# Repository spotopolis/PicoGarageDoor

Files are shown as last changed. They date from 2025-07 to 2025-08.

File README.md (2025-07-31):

# PicoGarageDoor
Simple garage door opener controlled wirelessly via webpage

# Intro
This is a simple device that allows you to add wireless functionality to garage door control.
This project was a result of being a motorcycle rider and wanting to be able to open/close the garage to pull the bike in/out without having to either walk back into the house to open/close the garage or press the paired garage door controller button attached to the sun visor in my car. I do not have a garage door button panel outside of my garage, so I made this simple device to access the garage door from my phone while within my homes WiFi signal range.

# Parts list

Required:

Raspberry Pi Pico W [from Microcenter](https://www.microcenter.com/product/687384/raspberry-pi-pico-2-w) (( Should also work with a Pico 2W but has not been tested ) $6.99 USD at the time of writing )

Arduino v5 relay [from MicroCenter](https://www.microcenter.com/product/659887/inland-single-5v-relay-module-for-arduino) ($1.99 USD at the time of writing)

Project can be completed for under $10 USD with just these two components and some spare wire.
#

Optional:

To make the build a litle cleaner, use GPIO headers and some jumper wires.

Jumper wires [from Microcenter](https://www.microcenter.com/product/412198/leo-sales-ltd-jumpers,-premium-6-f-f,-50-wires) ( $14.99 USD at the time of writing )

GPIO right-angle header(s) [from Microcenter](https://www.microcenter.com/product/475249/schmartboard-inc-01-spacing-40-single-row-right-angle-headers-10-pack) ( $7.99 USD at the time of writing )

# Function
The PicoW hosts a small basic webserver via the code below:



This in turn serves the following webpage:

GDoor

The blue "Open/Close" button acts as a momentary switch to trigger a 5v relay attached directly to the PicoW via GPIO.

This function is handled here:



#

I discovered that during a power outage or power flicker during a storm, while the WiFi network and PicoW would come back online after power is restored, the PicoW would lose connection to the network and therefor could not host the webpage to interact with. It would only come back up if I power cycled the PicoW again by hand. So to try and fix this, I have also included some basic logic to test if the connection to the gateway is active, if it is not, it will reboot the PicoW to try and reestablish a connection.

The PicoW will wait initially 60 seconds on first boot before testing that the network is active to give the device time to connect. After 60 seconds, the PicoW will start to ping the gateway every 30 seconds. If the ping attempt fails, it will retry to ping the gateway 2 more times (3 in total) before triggering the reboot. This is to help mitigate any temp signals issues / interference along with the PicoW's lack of power to reboot on a false positive signal interruption. This code is handled here:



and here:



# Setup

Before uploading the main.py to the PicoW, edit the file at lines 7, 8, and 9. Fill in your SSID, password, and gateway IP. Thonny or NotePad++ can be used for the edits.



Connections between the PicoW and relay are:

PicoW: VBUS <----> Relay: V

PicoW: GND  <----> Relay: G

PicoW: GP18 <----> Relay: S

#

Connect any 5v 1a USB charger to the PicoW's micro-USB port to power it on. Once the PicoW is powered on, it should get a local IP address assigned via DHCP from your firewall/router. You will want to log into your firewall/router and assign the PicoW a static IP address to make sure it doesn’t change on you and is always at the IP address you are expecting.

Once you select and set a static IP address for the PicoW in your firewall/router, power cycle the PicoW so it connects to your network with the newly assigned static IP.

Open a web browser on any device connected to the same WiFi network as the PicoW and browse to that static IP address. You should see the same page that I showed above under the "Function" section of this page. Tap or click the blue "Open/Close" button to verify the relay is triggering. You should hear it click on and then off while also getting an accompanying red LED to flash on the relay. If so, you are all set and ready to disconnect and attach it to your existing garage door button.

#

gdoor3

The relay can then be connected to your existing 2 wire garage door button via jumpers so that the button can still function while the relay is attached.
All this device is doing is acting like a 2nd garage door button attached to the same door. The garage door button is a momentary switch that seperates ( or bridges ) the connection between the two wires. By running jumper wires from the existing button to the relay, you are allowing a second button/switch ( the relay ) to trigger this function as well. Only instead of a physical button press, it is done via touchscreen on a mobile device on a private LAN hosted wepbage.

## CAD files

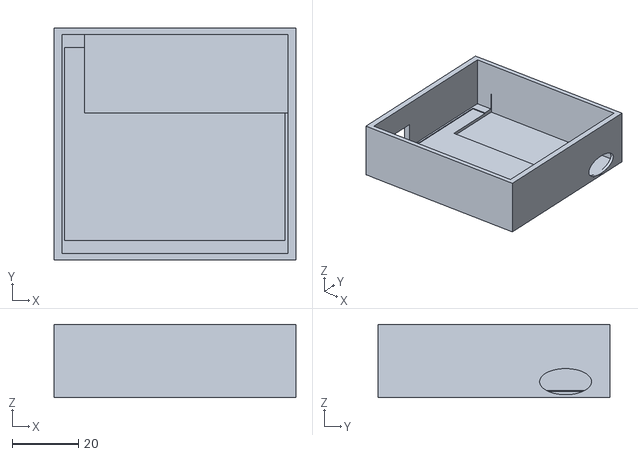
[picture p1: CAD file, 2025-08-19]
Box_Obj_Part.stl
72.9 x 69.8 x 22.0

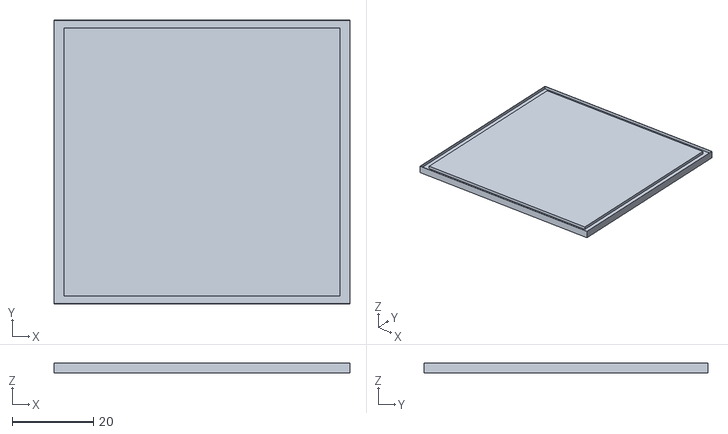
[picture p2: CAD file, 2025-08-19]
Lid_Obj_Part.stl
73.0 x 70.0 x 2.50

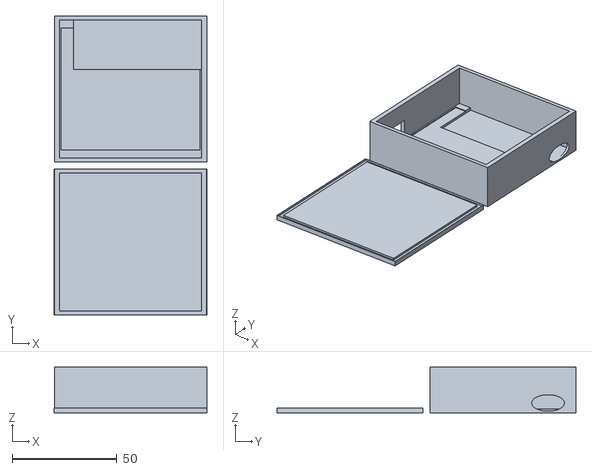
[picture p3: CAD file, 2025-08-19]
PicoW_Relay_Box_AIO.stl
73.0 x 143.0 x 22.0

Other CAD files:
PicoW_Relay_Box_ProjectFile.3mf

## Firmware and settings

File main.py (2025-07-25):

from machine import Pin, reset, Timer
import network
import time
import usocket as socket

# Wi-Fi credentials
SSID = "YOUR_WIFI_NAME_HERE"
PASSWORD = "WIFI_PASSWORD_HERE"
GATEWAY_IP = "ROUTER_IP_ADDRESS_USUALLY_192.168.1.1_OR_SIMILAR"

# Relay and onboard LED setup
relay = Pin(18, Pin.OUT)
led = Pin("LED", Pin.OUT)

# Flash LED on boot
led.on()
time.sleep(0.5)
led.off()

# Connect to Wi-Fi
wlan = network.WLAN(network.STA_IF)
wlan.active(True)
wlan.connect(SSID, PASSWORD)

# Wait up to 60s for Wi-Fi
start = time.time()
while wlan.status() != 3 and (time.time() - start) < 60:
    print("Waiting for Wi-Fi...")
    time.sleep(1)

if wlan.status() != 3:
    print("Wi-Fi failed. Soft rebooting...")
    reset()
else:
    print("Connected. IP:", wlan.ifconfig()[0])
time.sleep(5)

# Gateway ping check
def ping(ip=GATEWAY_IP, timeout=3):
    try:
        sock = socket.socket()
        sock.settimeout(timeout)
        sock.connect((ip, 80))
        sock.close()
        return True
    except:
        return False

# Schedule reboot
def delayed_reboot(timer):
    print("Soft rebooting...")
    s.close()
    reset()

# Web UI content
def web_server():
    html = """<html><head><meta name="viewport" content="width=device-width, initial-scale=1">
    <style>body{font-family:Arial;text-align:center;margin:0;padding-top:30px;}
    .button{display:inline-block;width:200px;height:68px;background-color:#2196F3;
    color:white;border:none;border-radius:34px;font-size:24px;cursor:pointer}</style>
    <script>
    function pressButton() {
        var xhr = new XMLHttpRequest();
        xhr.open("GET", "/?relay=off", true);
        xhr.send();
        setTimeout(function() {
            xhr.open("GET", "/?relay=on", true);
            xhr.send();
        }, 500);
    }
    </script></head><body>
    <h1>Garage Door Control</h1>
    <button class="button" onclick="pressButton()">Open/Close</button>
    </body></html>"""
    return html

# Start web server
s = socket.socket()
s.setblocking(False)
s.bind(('', 80))
s.listen(1)

fail_count = 0
max_failures = 3
last_ping = time.time()

try:
    while True:
        # Periodic ping
        if time.time() - last_ping > 30:
            if ping():
                print("Ping OK")
                fail_count = 0
            else:
                print("Ping failed")
                fail_count += 1
                if fail_count >= max_failures:
                    print("Too many failures. Reboot scheduled.")
                    Timer(-1).init(mode=Timer.ONE_SHOT, period=3000, callback=delayed_reboot)
            last_ping = time.time()

        try:
            conn, addr = s.accept()
            conn.settimeout(3)
            print("Connection from", addr)
            request = conn.recv(1024)
            print("Request:", request)

            if b"/?relay=on" in request:
                relay.value(0)
                print("RELAY ON")
            elif b"/?relay=off" in request:
                relay.value(1)
                print("RELAY OFF")

            response = web_server()
            conn.send("HTTP/1.1 200 OK\r\nContent-Type: text/html\r\n\r\n")
            conn.sendall(response)
            conn.close()

        except OSError:
            pass

except KeyboardInterrupt:
    print("Interrupted by user. Closing socket...")
    s.close()
    raise

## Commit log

2025-07-25 Update README.md
    Currently writing up instructions for use
2025-08-19 3D print files for simple box
    .STL and .3MF files added to 3D print a simple box just large enough to house the PicoW and relay. The lid is designed to friction fit.
    These were prepared in Bambu Studio and printed on a Bambu A1, but should easily print on any printer.
    Printed in PLA
    0.4mm Nozzle
    0.12mm Quality
    25% Sparse Infill
    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
    [Box_Obj_Part.stl, Lid_Obj_Part.stl, PicoW_Relay_Box_AIO.stl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]
